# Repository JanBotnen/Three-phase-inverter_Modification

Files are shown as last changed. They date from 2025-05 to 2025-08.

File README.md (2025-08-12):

# Three-phase-inverter_Modification

**Design and implementation of a three-phase inverter with SPWM and SVPWM, prepared for future PMSM control.**

## Background
This project focuses on the continued development and modification of a three-phase DC-to-AC converter, utilizing the Space Vector Pulse Width Modulation (SV-PWM) algorithm.
The inverter was originally designed and built by a previous bachelor group at the Western Norway University of Applied Sciences, and later further refined by another group who successfully reduced the physical footprint of the design.

Their thesis can be found at:
Version 1 : [HVL Open](https://hdl.handle.net/11250/3105460)
Version 2 : [HVL Open](https://hdl.handle.net/11250/3147156)

## About the Project

Building upon their work, our bachelor group aimed to prepare the inverter for future implementation of Field Oriented Control (FOC).  
Throughout this project, our primary goal has been to implement current measurement on all three phases and enable encoder input handling for rotor position feedback.

Our thesis can be found at: 
https://hdl.handle.net/11250/3202875

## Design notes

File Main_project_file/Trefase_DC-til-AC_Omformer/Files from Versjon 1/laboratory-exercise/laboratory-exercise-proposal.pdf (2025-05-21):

# Lab - 2-nivå trefase DC/AC-omformar¹

## Emnekode: ELE119

## Emnenamn: Kraftelektronikk

## Haust 2023

Labansvarleg: Lars M. Ekroll lme@hvl.no

Emneansvarlig: Eirik Haustveit
| ehau@hvl.no

Utlevert:
dd.mm.åååå

Frist:
dd.mm.åååå
Gjennomføring:
dd.mm.åååå

Denne laboratorieoppgåva dekker grunnleggande praktisk bruk av ein 2-nivå trefase DC/AC-omformar.

Spenningane og straumane som skal nyttast i oppgåva er moderate, men framleis på eit nivå som medfører

fare. Før arbeidet kan starta er det derfor obligatorisk med ein sikkerhetsgjennomgang for alle studentar

som skal gjennomføra oppgåva.

Figur 1: 150 V, livsfare.

- 2-nivå trefase-omformar
- Romvektormodulering - SV-PWM
- Sinuspulsbreiddemodulering - SPWM

1 Denne laboratorieoppgåva er utvikla av Marius Englund, Eirik Skorve Haugland og Ingrid Hovland, med utgangspunkt i ein mal utarbeidd av Eirik Haustveit.

Lab 1 | ELE119 - Kraftelektronikk | Haust 2023

## 1 Introduksjon

Denne laboratorieoppgåva dekker 2-nivå trefase-omformar. Oppgåva er strukturert i 3 delar:

1. Forarbeid: Her skal ein berekne nokre aktuelle parameter. I tillegg skal ein simulera berekna verdiar. Resultata frå berekningar og simuleringar skal noterast i oversiktstabellen.
2. Laboratoriearbeid: Her skal ein utføre oppkoplinga, samt måling på dei fysiske modellane. Det vil være ein stor fordel om ein har gjort seg godt kjent med ein simuleringsmodell og verktøya i forkant. Grunnleggande forståing for dei to modulasjonsteknikkane SPWM og SV-PWM er og ein stor fordel. Ein skal samle måleresultat i all hovudsak ved hjelp av oscilloskop. På oscillioskopet har ein verktøy som er kjent frå Simulink, som å måla verdiar som RMS, snitt, peak-peak, FFT m.m. Ein skal også lagre datasett som CSV-filer for å kunne etterbehandla dei i Matlab. Her er det viktig at ein organiserer arbeidet, slik at ein har kontroll på kva målingar som ligg i eit gitt datasett.
3. Etterarbeid: I etterarbeidet skal ein samanlikne utrekna, simulerte og fysiske måleresultat og studere avvika som ev. viser seg. Ein skal og tolke datasett frå laboratoriearbeidet.

Arbeidet skal oppsummerast i ein enkel rapport som dokumenter dei ulike delane av oppgåva.

### 1.1 Føresetnader

Arbeidet blir utført på spenningssatt anlegg med maksimal spenning 230 V. Då dette er eit spenningsnivå som har skadepotensial for både personar og utstyr, er ein tryggleiksgjennomgang med ansvarleg for elkraft-laboratoriet, Lars M. Ekrol påkrevd før den praktiske delen av oppgåva kan gjennomførast.

### 1.2 Utstyr

Under fylgjer ei liste over utstyr som blir gjort tilgjengeleg for den praktiske gjennomføringa. Noter utstyrsnummeret du har brukt i tabell 1. Om det er avvik frå ditt oppsett skal dette avviket noterast i din rapport.

Tabell 1: Liste over utstyr til lab

Utstyr | Skildring | Utstyrsnr | Kommentar
Trafo | 2 kVA trafo, 220/133 V
Brytar | Brytar i tilførsel
Brytar | Brytar i last
Sikring | 3 fase, 2/6 A
Koblingsboks | For tilkopling og måling
Kraftmodul | 2-nivå trefase-omformar
Spenningsprobe 1 | Micsig DP1003
Spenningsprobe 2 | Micsig DP1003
Strømtang 1 | Micsig CP2100A
Strømtang 2 | Micsig CP2100A
Multimeter | Hioki DT4282
| Koplingsleidningar med bananplugg
Effektmotstand | Belastningsmotstand
Effektmotstand | Straumbegrensingsmotstand for kondensator

Side 1 av 8

Lab 1 | ELE119 - Kraftelektronikk | Haust 2023

### 1.3 Måleinstrument

For å gjennomføra denne laboratorieoppgåva er det nødvendig å ha kjennskap til dei måleinstrumenta ein skal nytta. I all hovudsak skal oscilloskop nyttast til målingane, men det kan og vera aktuelt å foreta enkelte målingar med multimeter. Figur figur 2 viser oscilloskopet som skal nyttast. Det føresett grunnleggande forkunnskap i å bruka oscilloskopet, som justering av skallering, tid, størrelse, trigger og liknande. Vedlegg A gir ei enkel innføring i korleis ein stillar in probar, samt korleis ein hentar ut relevante målingar.

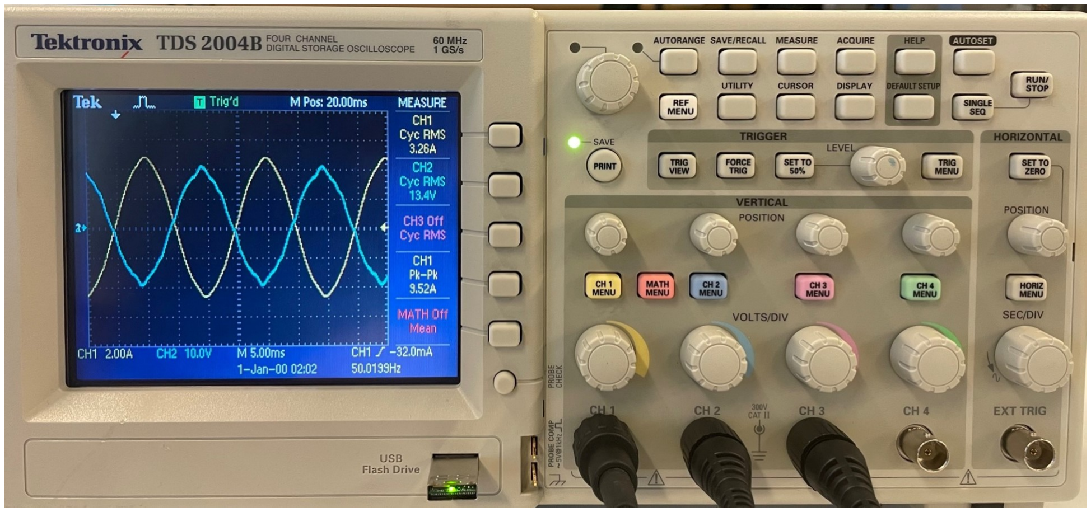
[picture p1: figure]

Figur 2Bilde av oscilloskop, Tektronix TDS 2004B

Side 2 av 8

Lab 1 | ELE119 - Kraftelektronikk | Haust 2023

## 2 2-nivå trefase-omformar

Oppgåve 1
I denne oppgåva skal de gjera målingar på ein 2-nivå trefase-omformar. Omformaren består av ein DC-link og seks transistorar som kan verta styrt med forskjellige modulasjonsteknikkar. I denne oppgåva skal dei to modulasjonsteknikkane sinuspulsbreiddemodulasjon (SPWM) og romvektormodulasjon (SV-PWM) samanliknast.

Tilført spenning Us = 150 V med frekvensen f1 = 50 Hz.

Forarbeid:
(a) Utfør berekning av verdiar gitt i tabell 2 for SPWM og SV-PWM.
(b) Simuler verdiane gitt i tabell 2.

Laboratoriearbeid:
Dei akutelle “measure” verdiane frå skopet skal noterast i tabell 2.
(a) Kontroller at du har tilgong på nødvendig utstyr, og kople opp omformaren mot last. Alle
| målingane skal gjerast for både SPWM og SV-PWM.
(b) Skru på DC-link spenning og svitsjing i mikrokontroller ved å trykke start på kortet. Observer tilført og avgitt spenning på oscilloskopet. Du skal bruka “measure” funksjonen i skopet til å finna frekvens, snitt, peak-peak og RMS verdi av målingane. Vidare skal du lagra eit datasett av målingane til ein minnepinne. For referanse skal PWM frå mikrokontroller vera med på alle målingar frå skopet.
i. Foreta ei samtidig måling av tilført, samt avgitt spenning. Noter “measure” verdiane.
| ii. Foreta ei måling av tilført, samt avgitt straum. Noter “measure” verdiane.
iii. Foreta ei samtidig måling av tilført straum og spenning. Bruk “math” funksjonen i skopet til å finna effektkurva og ta snittet av denne kurva for å finna aktiv effekt. Noter “measure” verdiane.
iv. Foreta ei samtidig måling av avgitt straum og spenning. Bruk “math” funksjonen i skopet til å finna avgitt aktiv effekt. Noter “measure” verdien av snittet til den berekna effektkurva.
v. Mål det harmoniske innhaldet i spenning.

Etterarbeid:
(a) Vurder kva som er årsaka, dersom det er nokon ruter i tabellen som står tomme. Kvifor er dette verdiar som er vanskelig å berekna, eller å måla fysisk? Dersom du har fyllt ut heile tabellen,
| treng du ikkje svare på denne oppgåva.
(b) Vurder årsaker til avvik mellom berekningar og fysiske målingar. Ta omsyn til toleransar i
| måleinstrument, og ikkje-ideelle eigenskapar ved diodane.
(c) Samalikn kurvene frå datasetta til SPWM og SV-PWM. Kva er årsaken til likheitar og ulikheitar?
(d) Samanlikn målte og simulerte resultat av dei to modulasjonsteknikkane.

Side 3 av 8

Lab 1 | ELE119 - Kraftelektronikk | Haust 2023

Tabell 2. Samanlikning mellom berekna, simulerte, og målte verdiar

| | | SPWM | | | SV-PWM
Storleik | Skildring | Kalk. | Sim. | Målt | Kalk. | Sim. | Målt
U¯
d | Avgitt snittspenning
Ud | Avgitt RMS spenning
¯Id | Avgitt snittstraum
∆Ud | Rippel i avgitt spenning
Us | Tilført RMS spenning | 150 V | 150 V | | 150 V | 150 V
Is | Tilført RMS straum
Is1 | Grunnharmonisk RMS straum
Is3 | RMS av 3 harmoniske i tilført straum
THDi | THD i tilført straum
Pd | Avgitt aktiv effekt | X | | | X
Ps | Aktiv effekt frå Us | X | | | X
PF | Total effektfaktor | X | | | X

Side 4 av 8

## A Innstilling og bruk av oscilloskop

Dette vedlegget gir ei kort inføring i det oscilloskopet, samt dei måleprobane ein skal nytta i denne laboppgåva.

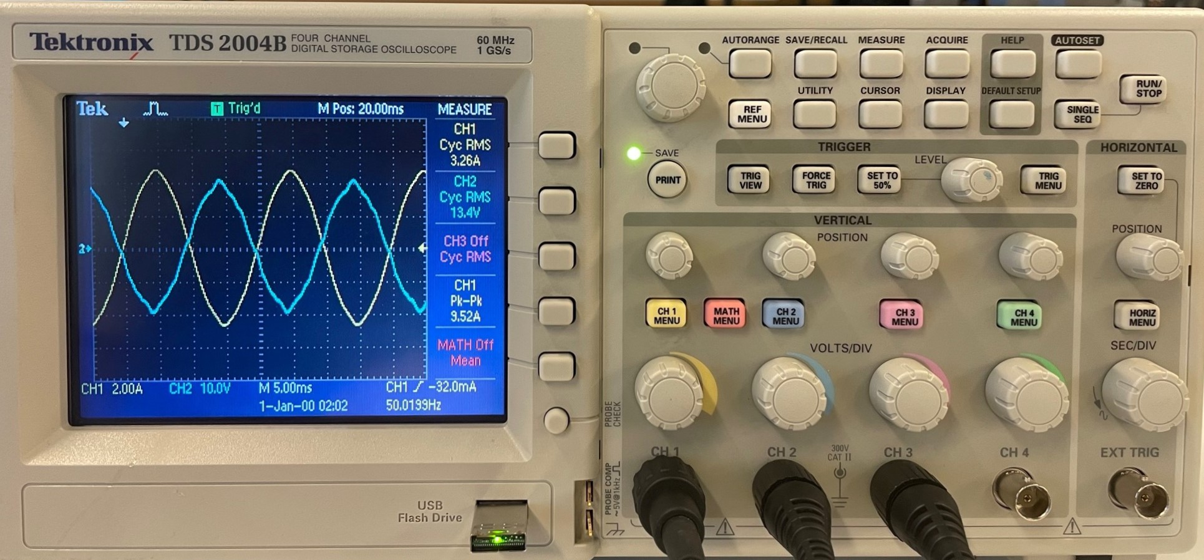
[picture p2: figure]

Figur 3Bilde av oscilloskop, Tektronix TDS 2004B

A.1 Differensialprobe for spenningsmåling

Differensialproben Micsig DP10013 skal brukast til spenningsmåling og kan operera opptil 1,3 kV. Proben kan stillast på 2 måleområder, X50/X500, og ein må velga det området som passar best for dei spenningane ein forventer å måla. For riktig avlesing på oscilloskopet må ein stilla det inn på det samme måleområdet som proben.

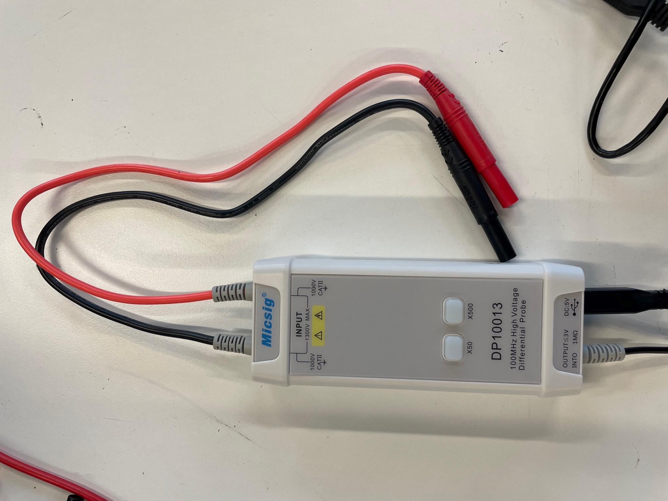
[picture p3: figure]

Figur 4Bilde av differensialprobe for spenningsmåling, Micsig DP1003

Frå kanal menyen “CH X MENU” får ein individuelle valg per kanal i sidemenyen. “Coupling”, skal vera DC. For spenningsproben velger ein “Voltage” og “Attenuation” 50X eller 500X avhengig av din probeinnstilling.

A.2 Tangamperemeter for straummåling

Straumtanga Micsig CP2100A skal brukast til straummåling og kan operere opptil 100 A. Proben kan stillast på 2 måleområder, 10 eller 100 A.
Frå kanal menyen “CH X MENU” får ein individuelle valg per kanal i sidemenyen. “Coupling”, skal vera DC. For straumtanga velger ein “Current” og “Scale” etter minste måleområde, 100 mV/A. Sjekk at straumtanga lyser på 10 A måleområde. Når skalering er utført kan ein nullstille straumtanga ved å trykke “Zero” og evt. justere DC-offset med pilene dersom den ikkje viser 0 A før du begynner å ta målingar.

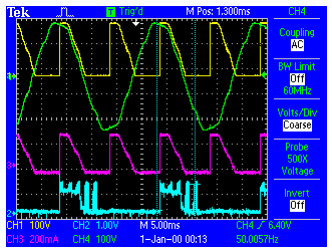
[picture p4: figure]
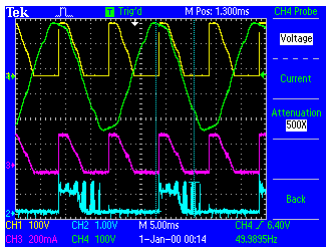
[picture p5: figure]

(a) Sidemeny etter valg av “CH X MENU”. | (b) Sidemeny etter valg av “Probe”

Figur 5Instilling av spenningsprobe

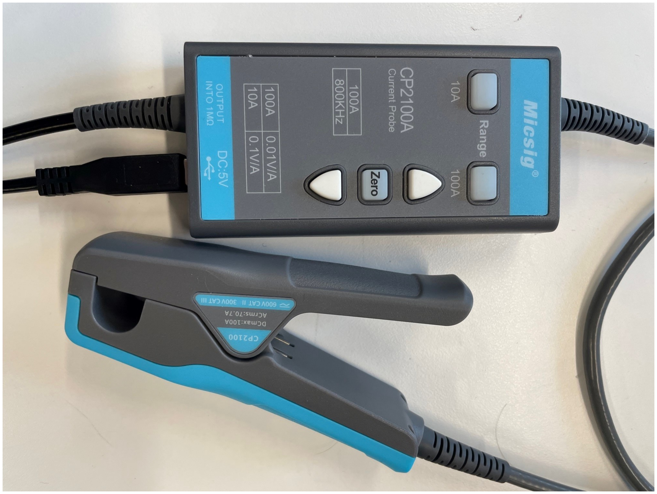
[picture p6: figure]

Figur 6Bilde av strømtang, Micsig CP2100A

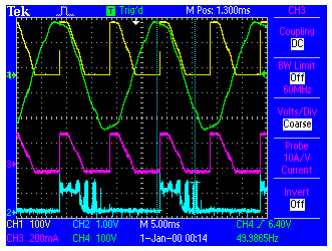
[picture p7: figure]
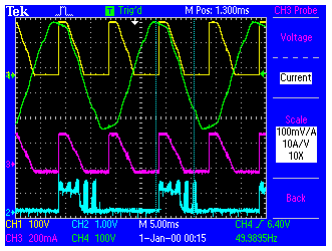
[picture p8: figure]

(a) Sidemeny etter valg av “CH X MENU” | (b) Sidemeny etter valg av “Probe”

Figur 7Instilling av straumtang

A.3 Målingar på skop

Oscilloskopet har ein “measure”-funksjon som kan gi oss forskjellige verdiar ut frå dei kurvene me måler. Denne funksjonen skal me nytta til å henta ut RMS, snitt, peak-peak og frekvens. For å definere målingar mot gitt kanal trykker ein på “measure” og velger målepunkt i sidemenyen. Frå sidemenyen velger ein spesifikk kanal og kan vidare definere kjelde, og målefunksjon.

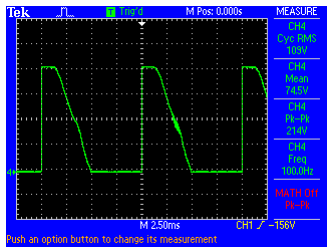
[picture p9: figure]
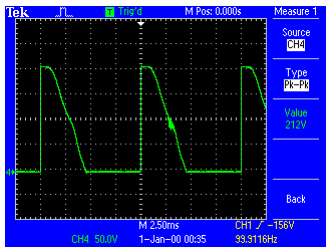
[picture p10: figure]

(a) Sidemeny etter valg av “Measure” | (b) Sidemeny etter valg av spesifik måling

Figur 8Instilling av målingar som RMS, snitt, peak-peak, frekvens med fleire

A.4 Bruk av “cursors” på skop

“Cursors” kan nyttast for å sjå dei forskjellige kurvene i relasjon til kvar andre, eller for å finna relasjonen mellom forskjellige punkt på den samme kurva. Ein kan avlesa distanse i tid, eller i spenning eller straum. For å aktivera trykker ein på “Cursors” og velger type og kanal. Ein velger mellom dei 2 målelinjene, “Cursors”, i sidemenyen og kan flytte disse individuelt med multi-purpose hjulet. Punktavlesning per målelinje kan lesast av samt differansen mellom dei 2 målelinjene.

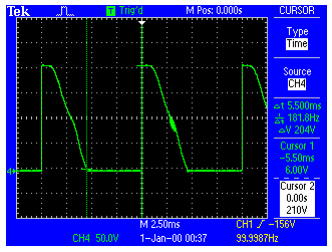
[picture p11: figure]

(a) Vertikale “Cursors” for punktavlesning og tidsdifferanse

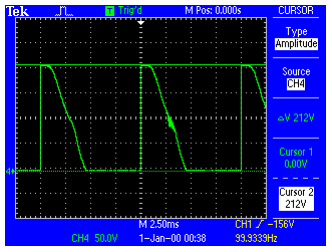
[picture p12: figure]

(b) Horistontale “Cursors” for punktavlesning og amplitudedifferanse

Figur 9Bruk av “Cursors” til måling av signal

A.5 Matte-funksjonar

Ein kan bruke scopet til å rekne ut samanhengar mellom kanalar samt gjera nokre analysar per kanal. For å berekne effekt kan ein multiplisere straum og spenning ved å trykker på “MATH MENU” ved å velge X i operasjon fra sidemenyen. Matte-funksjonen kan vidare hentast inn i “Measure” bildet
Ein kan og gjere måling av harmonisk spekter for ein kanal ved å trykker på “MATH MENU” ved å velge kilde referert til kanal, source, samt FFT frå sidemenyen. Ein kan i dette bildet bruke “Cursors” til å lese av frekvens/amplitude.
Figur 11 viser eit døme på FFT-bilde frå skopet.
FFT målingane på Tektronix TDS 2004B er oppgitt i desibel relativt til ei RMS spenning på 1 V. Den fylgjande formelen syner samanhengen mellom spenning og desibel:

dBV = 20 log
U

1 V
(1)

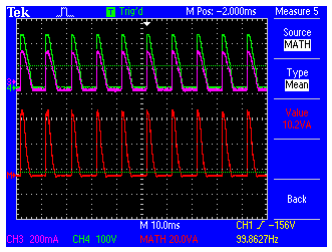
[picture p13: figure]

(a) Sidemeny og effektkurve etter valg av “Measure” mot mattefunksjon

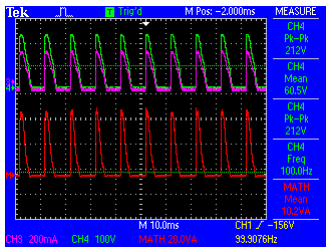
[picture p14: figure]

(b) Sidemeny inkludert målingar og mattefunksjon

Figur 10Bruk av mattefunksjon til å multiplisere straum og spenning

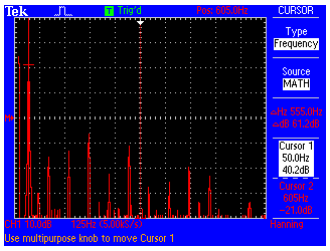
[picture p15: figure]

Figur 11FFT-måling

A.6 Total harmonisk forvrenging

Det er ikkje vanleg at oscilloskopet har innebygd støtte for berekning av total harmonisk forvrenging. Det er derimot mulig å berekna verdien frå dei harmoniske komponentane ein finn i spektrumsanalysatoren.

THDu =

p
U

2
2 + U

2
3 + U

2
4 + . . .
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
+ . . . | (2)

Differansen mellom den grunnharmoniske og ein overharmonisk komponent kan uttrykkast som:

dBc = 10 · log
P
Pc
(3)

Der P er den overharmoniske og Pc er den grunnharmoniske (carrier). Denne verdien kan normalt finnast ved å plassera ein "cursorpå den grunnharmoniske, og ein anna "cursorpå den overharmoniske komponenten som er av interesse. Verdien ein er ute etter er ofte uttrykt som ∆dB.

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
= 10

dBc
10

(5)

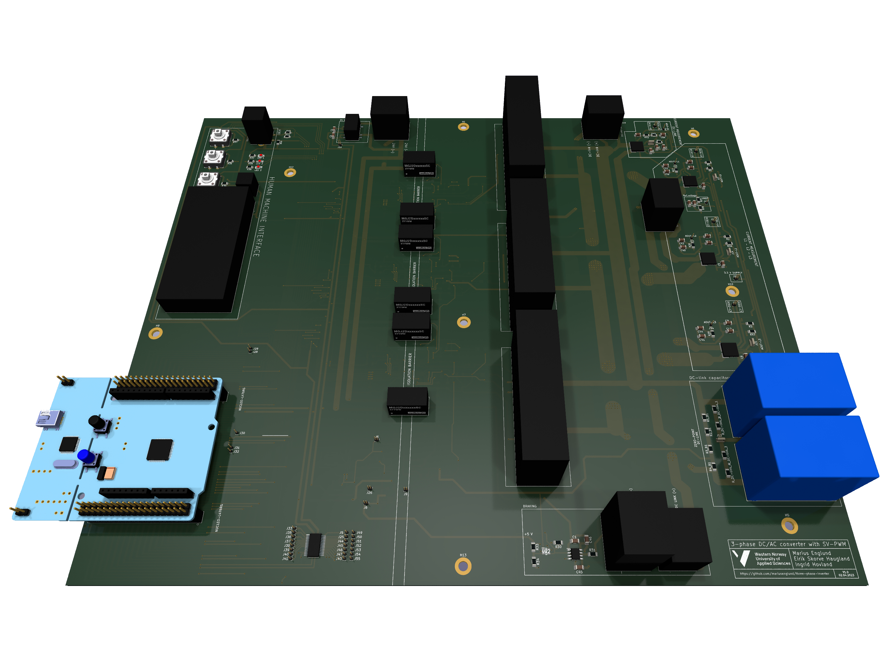
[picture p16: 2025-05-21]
Main_project_file/Trefase_DC-til-AC_Omformer/Files from Versjon 1/img/3d-model-front.png

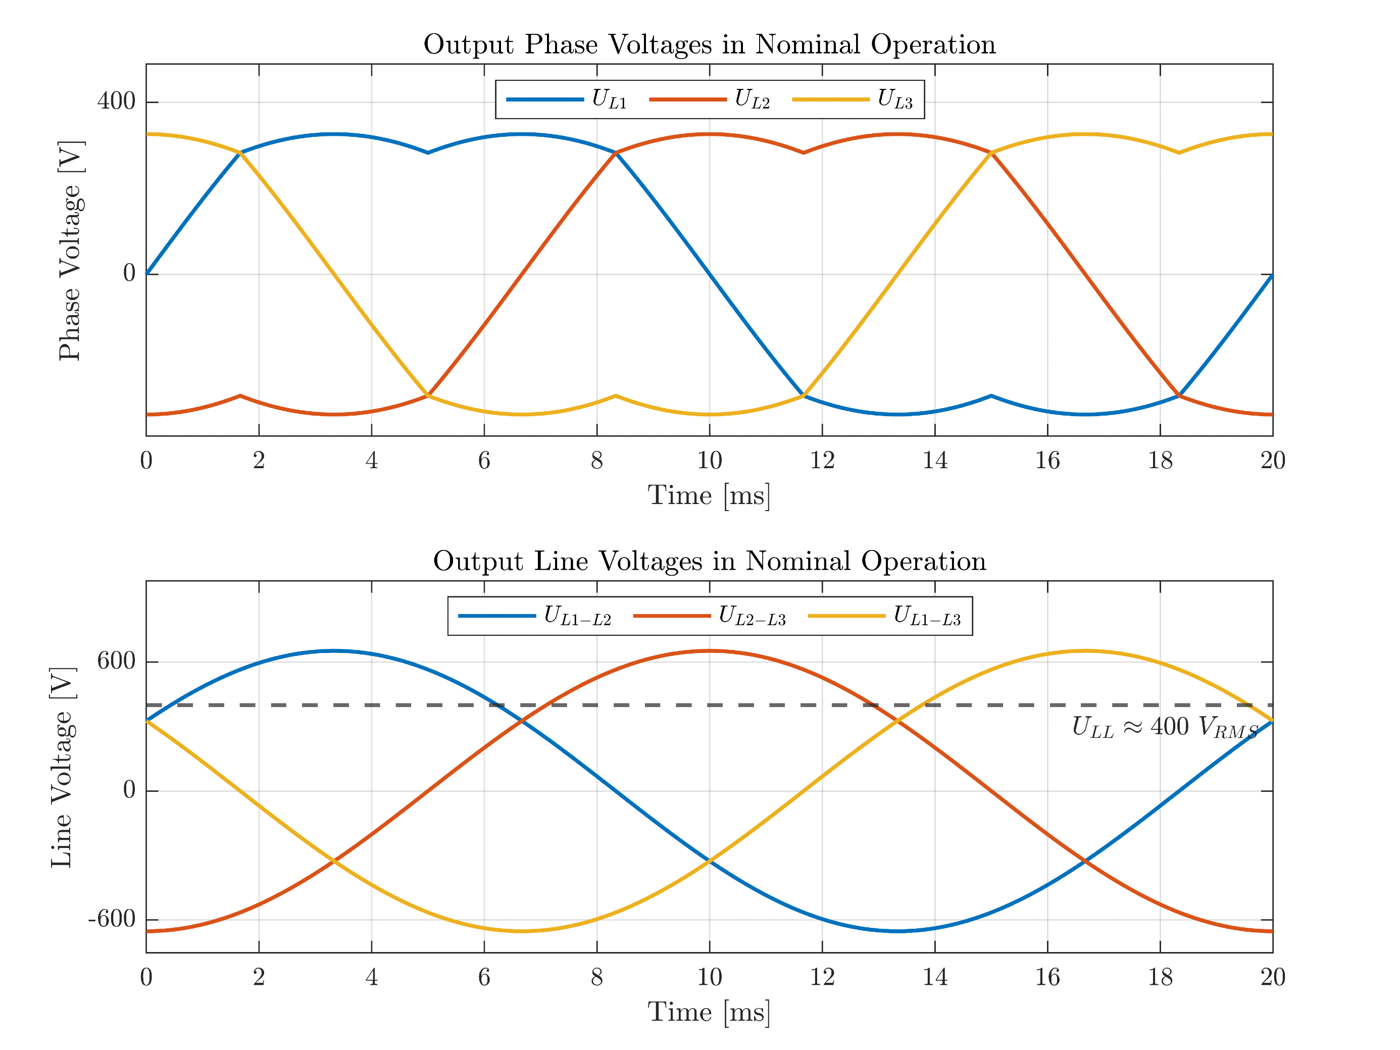
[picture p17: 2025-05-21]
Main_project_file/Trefase_DC-til-AC_Omformer/Files from Versjon 1/img/space-vector-voltages.png

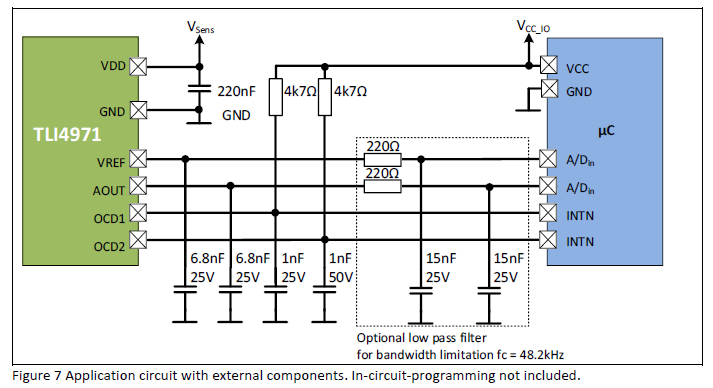
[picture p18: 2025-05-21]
Main_project_file/Trefase_DC-til-AC_Omformer/Files from Versjon 1/Koblingsskjemaer/Strømsensor_kobling.png

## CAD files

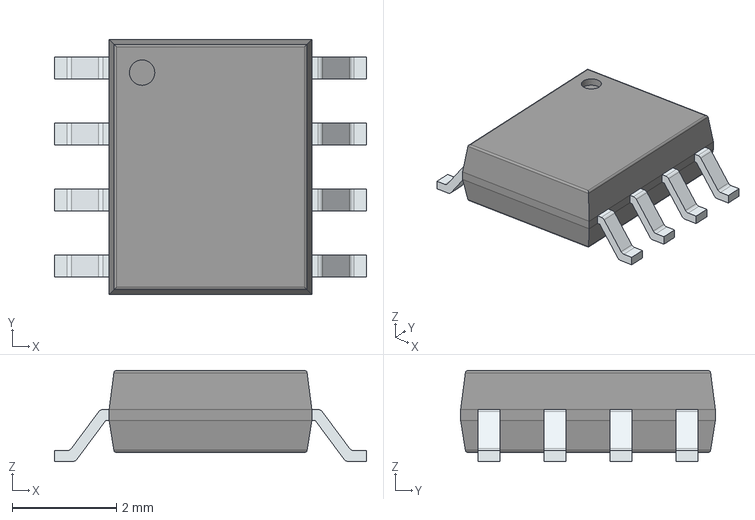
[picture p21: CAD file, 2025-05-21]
Main_project_file/Trefase_DC-til-AC_Omformer/pcb-design-files_v3/LIB-3D/IR2118SPBF.stp
6.00 x 4.90 x 1.75 mm
PinsArrayLR

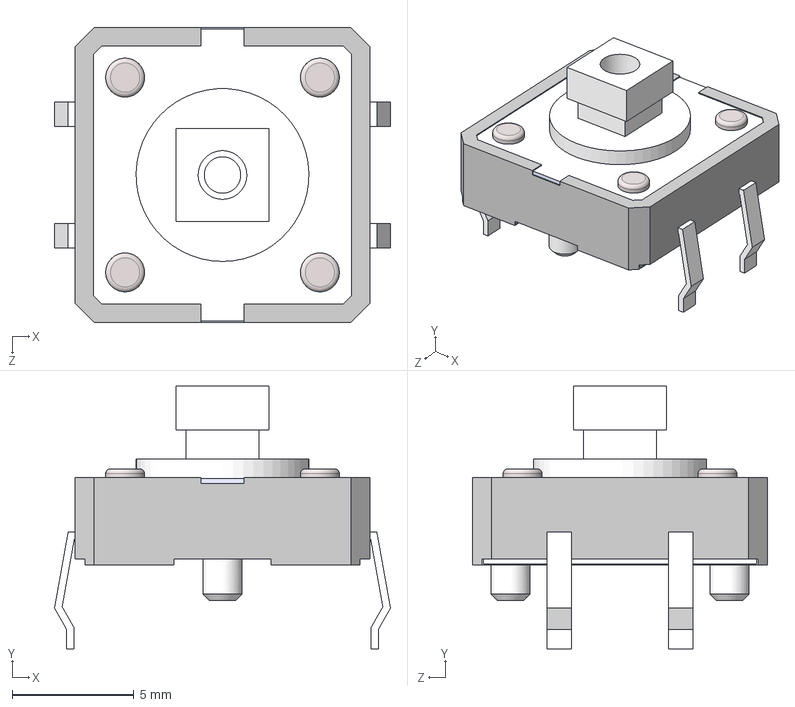
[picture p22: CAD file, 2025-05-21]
Main_project_file/Trefase_DC-til-AC_Omformer/pcb-design-files_v3/LIB-3D/B3F-5050.stp
13.8 x 10.8 x 12.1 mm

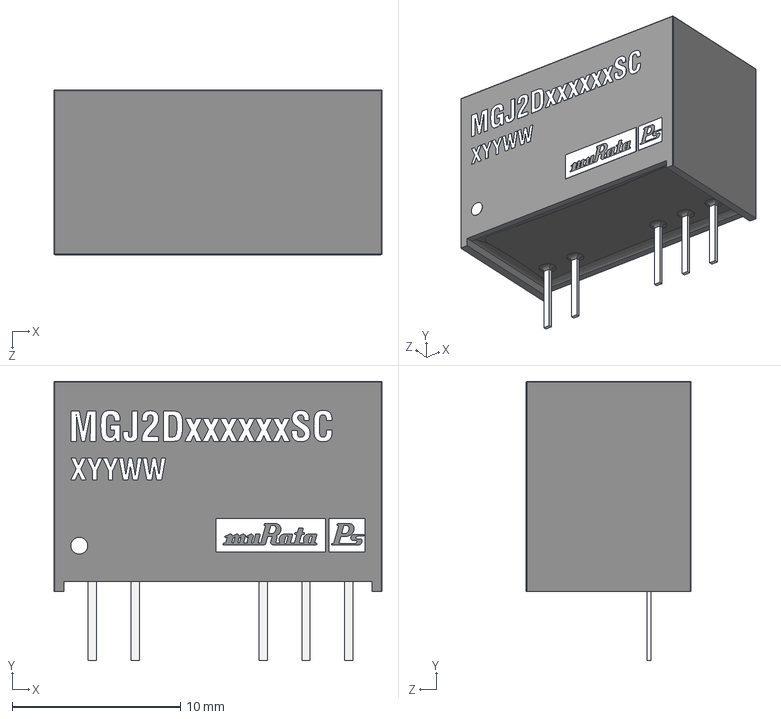
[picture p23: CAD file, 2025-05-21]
Main_project_file/Trefase_DC-til-AC_Omformer/pcb-design-files_v3/LIB-3D/MGJ2D241509SC.stp
19.5 x 16.6 x 9.82 mm

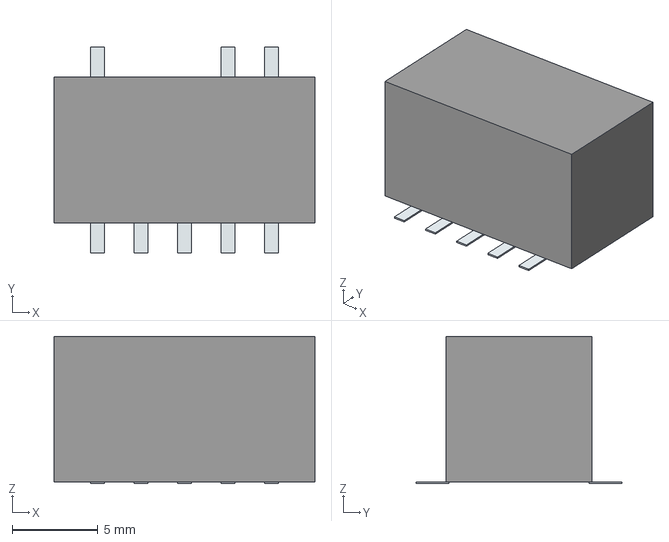
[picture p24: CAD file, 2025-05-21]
Main_project_file/Trefase_DC-til-AC_Omformer/pcb-design-files_v3/LIB-3D/MP-K7803T-500R3.stp
15.2 x 12.0 x 8.60 mm
Pins

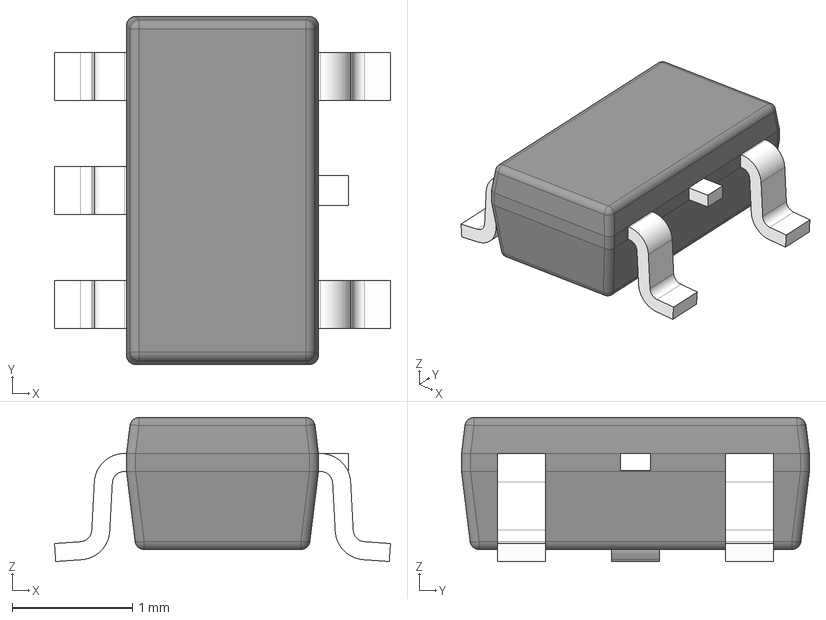
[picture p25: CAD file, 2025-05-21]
Main_project_file/Trefase_DC-til-AC_Omformer/pcb-design-files_v3/LIB-3D/LMV331M5.stp
2.80 x 2.90 x 1.20 mm
BODY-SOT
LEAD-SOT x 5
LEAD-DUMMY

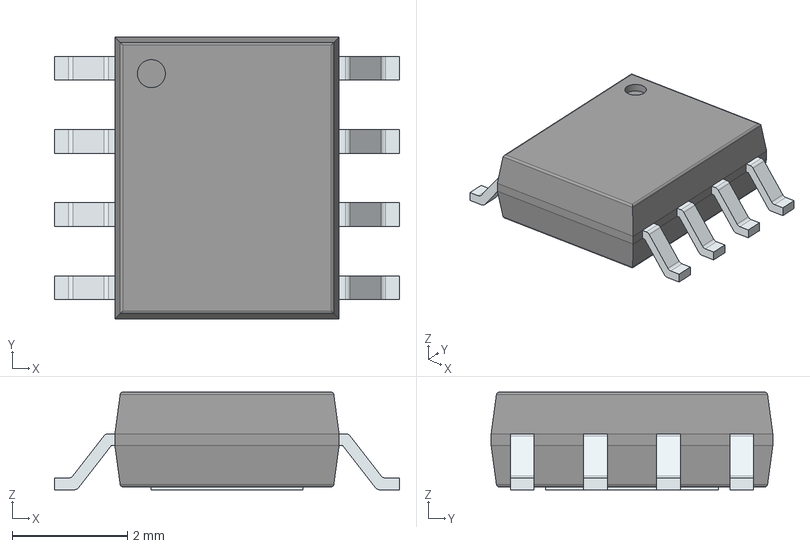
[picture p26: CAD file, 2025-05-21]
Main_project_file/Trefase_DC-til-AC_Omformer/pcb-design-files_v3/LIB-3D/TLS205B0EJV33XUMA1.stp
6.00 x 4.90 x 1.70 mm
PinsArrayLR
ThermalPad

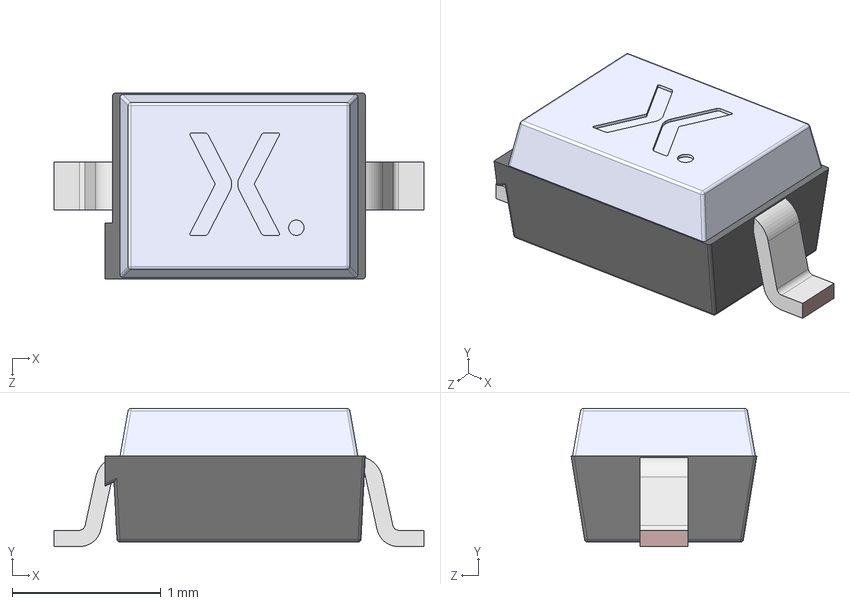
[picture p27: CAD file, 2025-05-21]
Main_project_file/Trefase_DC-til-AC_Omformer/pcb-design-files_v3/LIB-3D/Schottky-BAT165AX.stp
2.49 x 0.93 x 1.25 mm
SOD323 Lower body
SOD323 Lead x 2
SOD323 Upper body

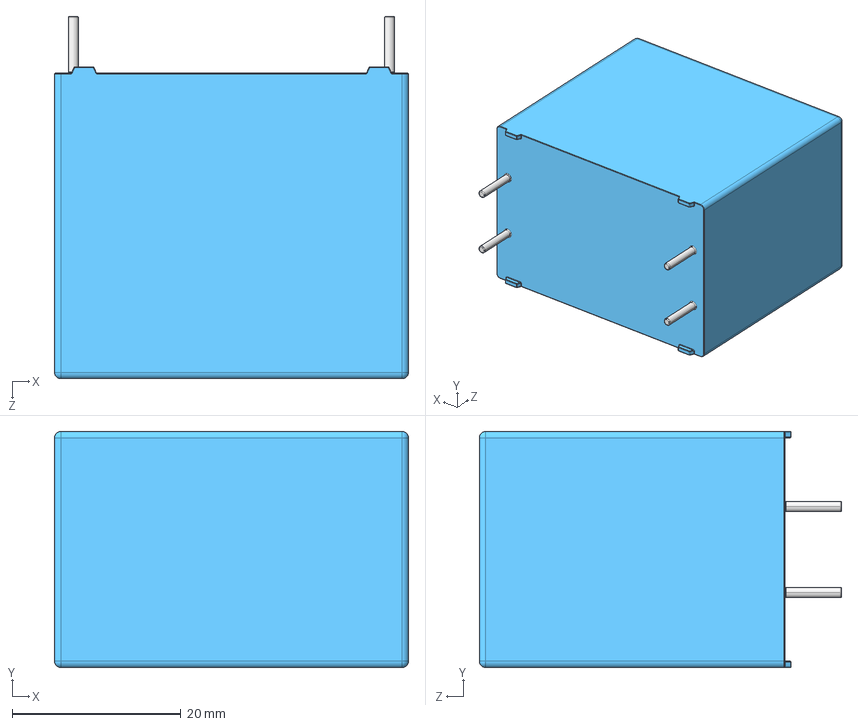
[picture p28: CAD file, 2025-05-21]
Main_project_file/Trefase_DC-til-AC_Omformer/pcb-design-files_v3/LIB-3D/DC-link-capacitor-B32776G0146K000.stp
42.0 x 28.0 x 43.0 mm

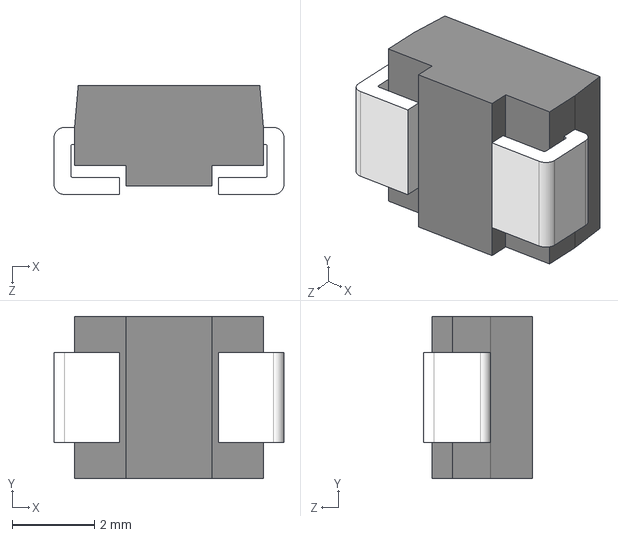
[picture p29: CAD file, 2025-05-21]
Main_project_file/Trefase_DC-til-AC_Omformer/pcb-design-files_v3/LIB-3D/Diode-STTH112U.stp
5.60 x 3.95 x 2.65 mm

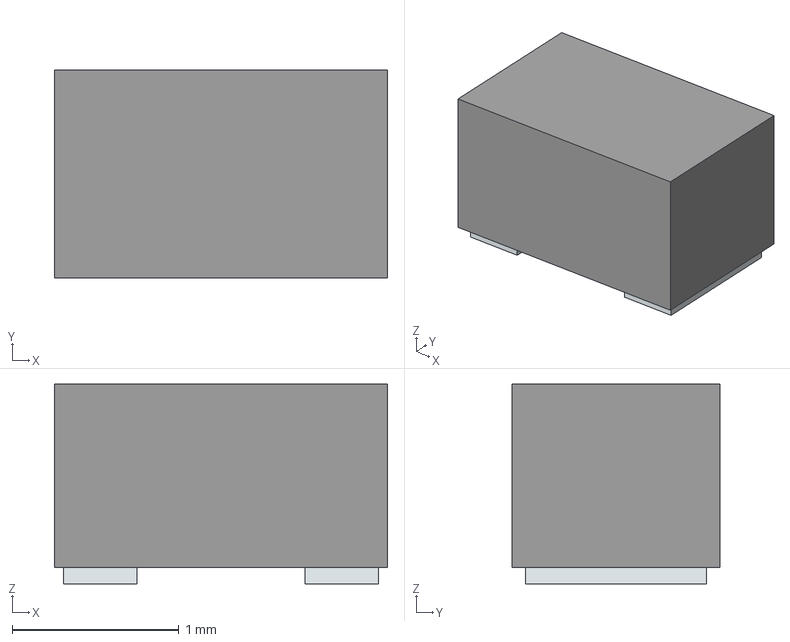
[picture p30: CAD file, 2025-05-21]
Main_project_file/Trefase_DC-til-AC_Omformer/pcb-design-files_v3/LIB-3D/LED_yellow_SML-LX0805SYC-TR.stp
2.00 x 1.25 x 1.20 mm
Pins

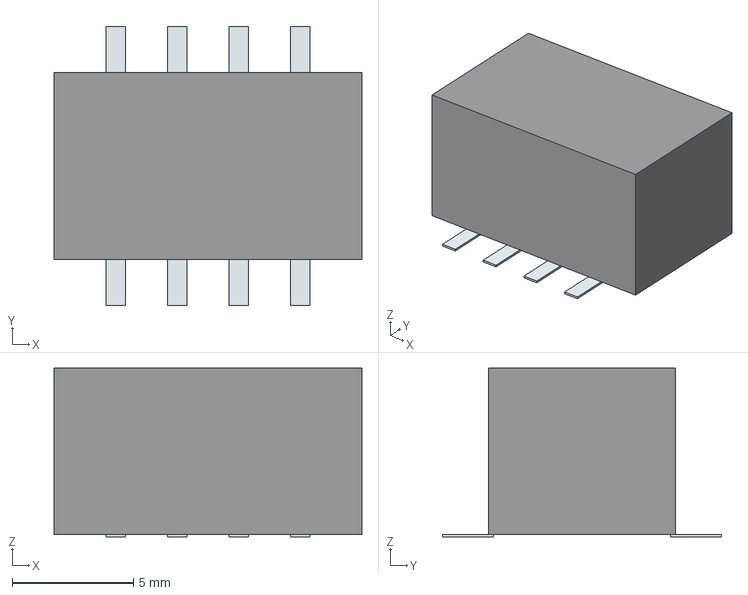
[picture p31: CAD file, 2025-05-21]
Main_project_file/Trefase_DC-til-AC_Omformer/pcb-design-files_v3/LIB-3D/NTE0505MC.stp
12.7 x 11.5 x 6.95 mm
Pins

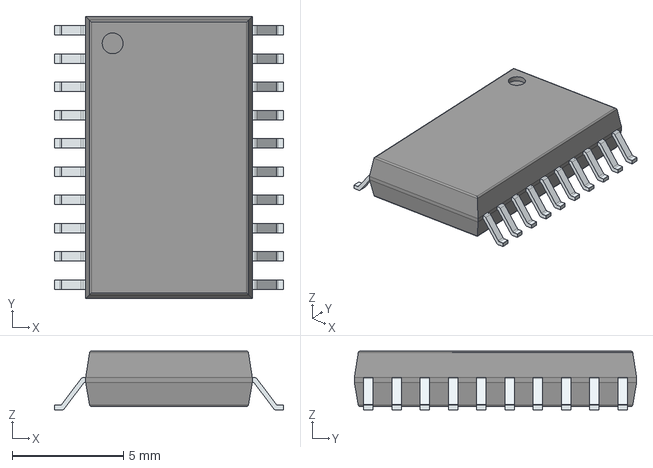
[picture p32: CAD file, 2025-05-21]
Main_project_file/Trefase_DC-til-AC_Omformer/pcb-design-files_v3/LIB-3D/1ED020I12FA2XUMA2.stp
10.3 x 12.7 x 2.65 mm
PinsArrayLR

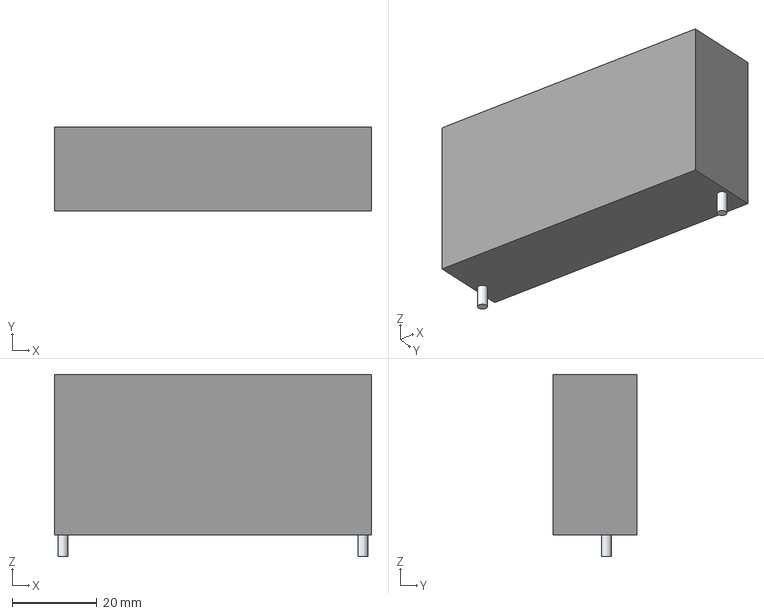
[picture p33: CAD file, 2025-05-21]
Main_project_file/Trefase_DC-til-AC_Omformer/pcb-design-files_v3/LIB-3D/Heatsink_C247-075-3AE.stp
75.0 x 19.9 x 43.1 mm
Leads x 2

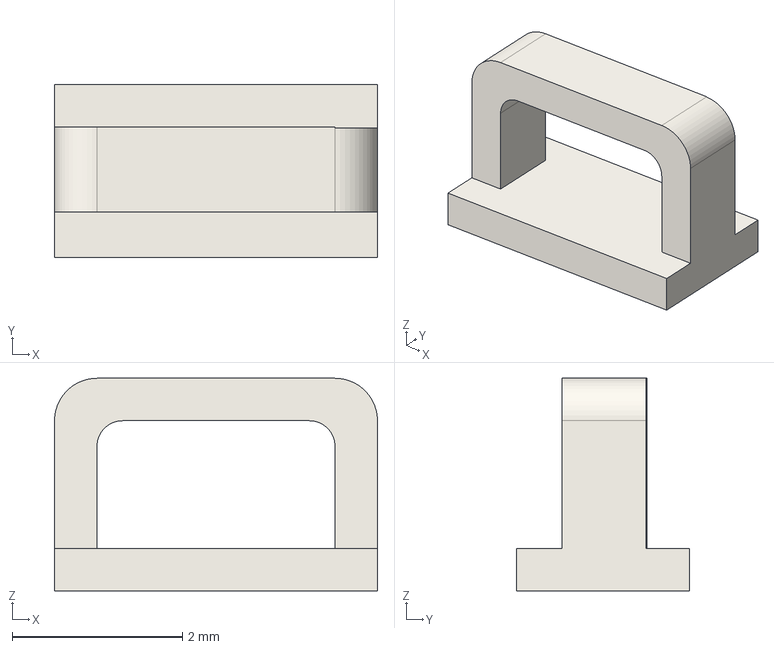
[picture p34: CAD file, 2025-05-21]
Main_project_file/Trefase_DC-til-AC_Omformer/pcb-design-files_v3/LIB-3D/Keystone - 5019 - PCB Test Point v1.step
3.80 x 2.03 x 2.50 mm

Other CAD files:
Main_project_file/Trefase_DC-til-AC_Omformer/pcb-design-files_v3/LIB-3D/C247-025-1VE.stp
Main_project_file/Trefase_DC-til-AC_Omformer/pcb-design-files_v3/LIB-3D/Encoder_EC12E2424407.stp
Main_project_file/Trefase_DC-til-AC_Omformer/pcb-design-files_v3/LIB-3D/OPA237NA_250.stp
Main_project_file/Trefase_DC-til-AC_Omformer/pcb-design-files_v3/LIB-3D/ACPL-C87B-000E.stp
Main_project_file/Trefase_DC-til-AC_Omformer/pcb-design-files_v3/LIB-3D/61304021821.stp
Main_project_file/Trefase_DC-til-AC_Omformer/pcb-design-files_v3/LIB-3D/74LV1T34GV-Q100H.stp
Main_project_file/Trefase_DC-til-AC_Omformer/pcb-design-files_v3/LIB-3D/Display_MC21605C6W-SPTLYI-V2.stp
Main_project_file/Trefase_DC-til-AC_Omformer/pcb-design-files_v3/LIB-3D/IKW40N120H3.stp
Main_project_file/Trefase_DC-til-AC_Omformer/pcb-design-files_v3/LIB-3D/LED_red_SML-LX0805SIC-TR.stp
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

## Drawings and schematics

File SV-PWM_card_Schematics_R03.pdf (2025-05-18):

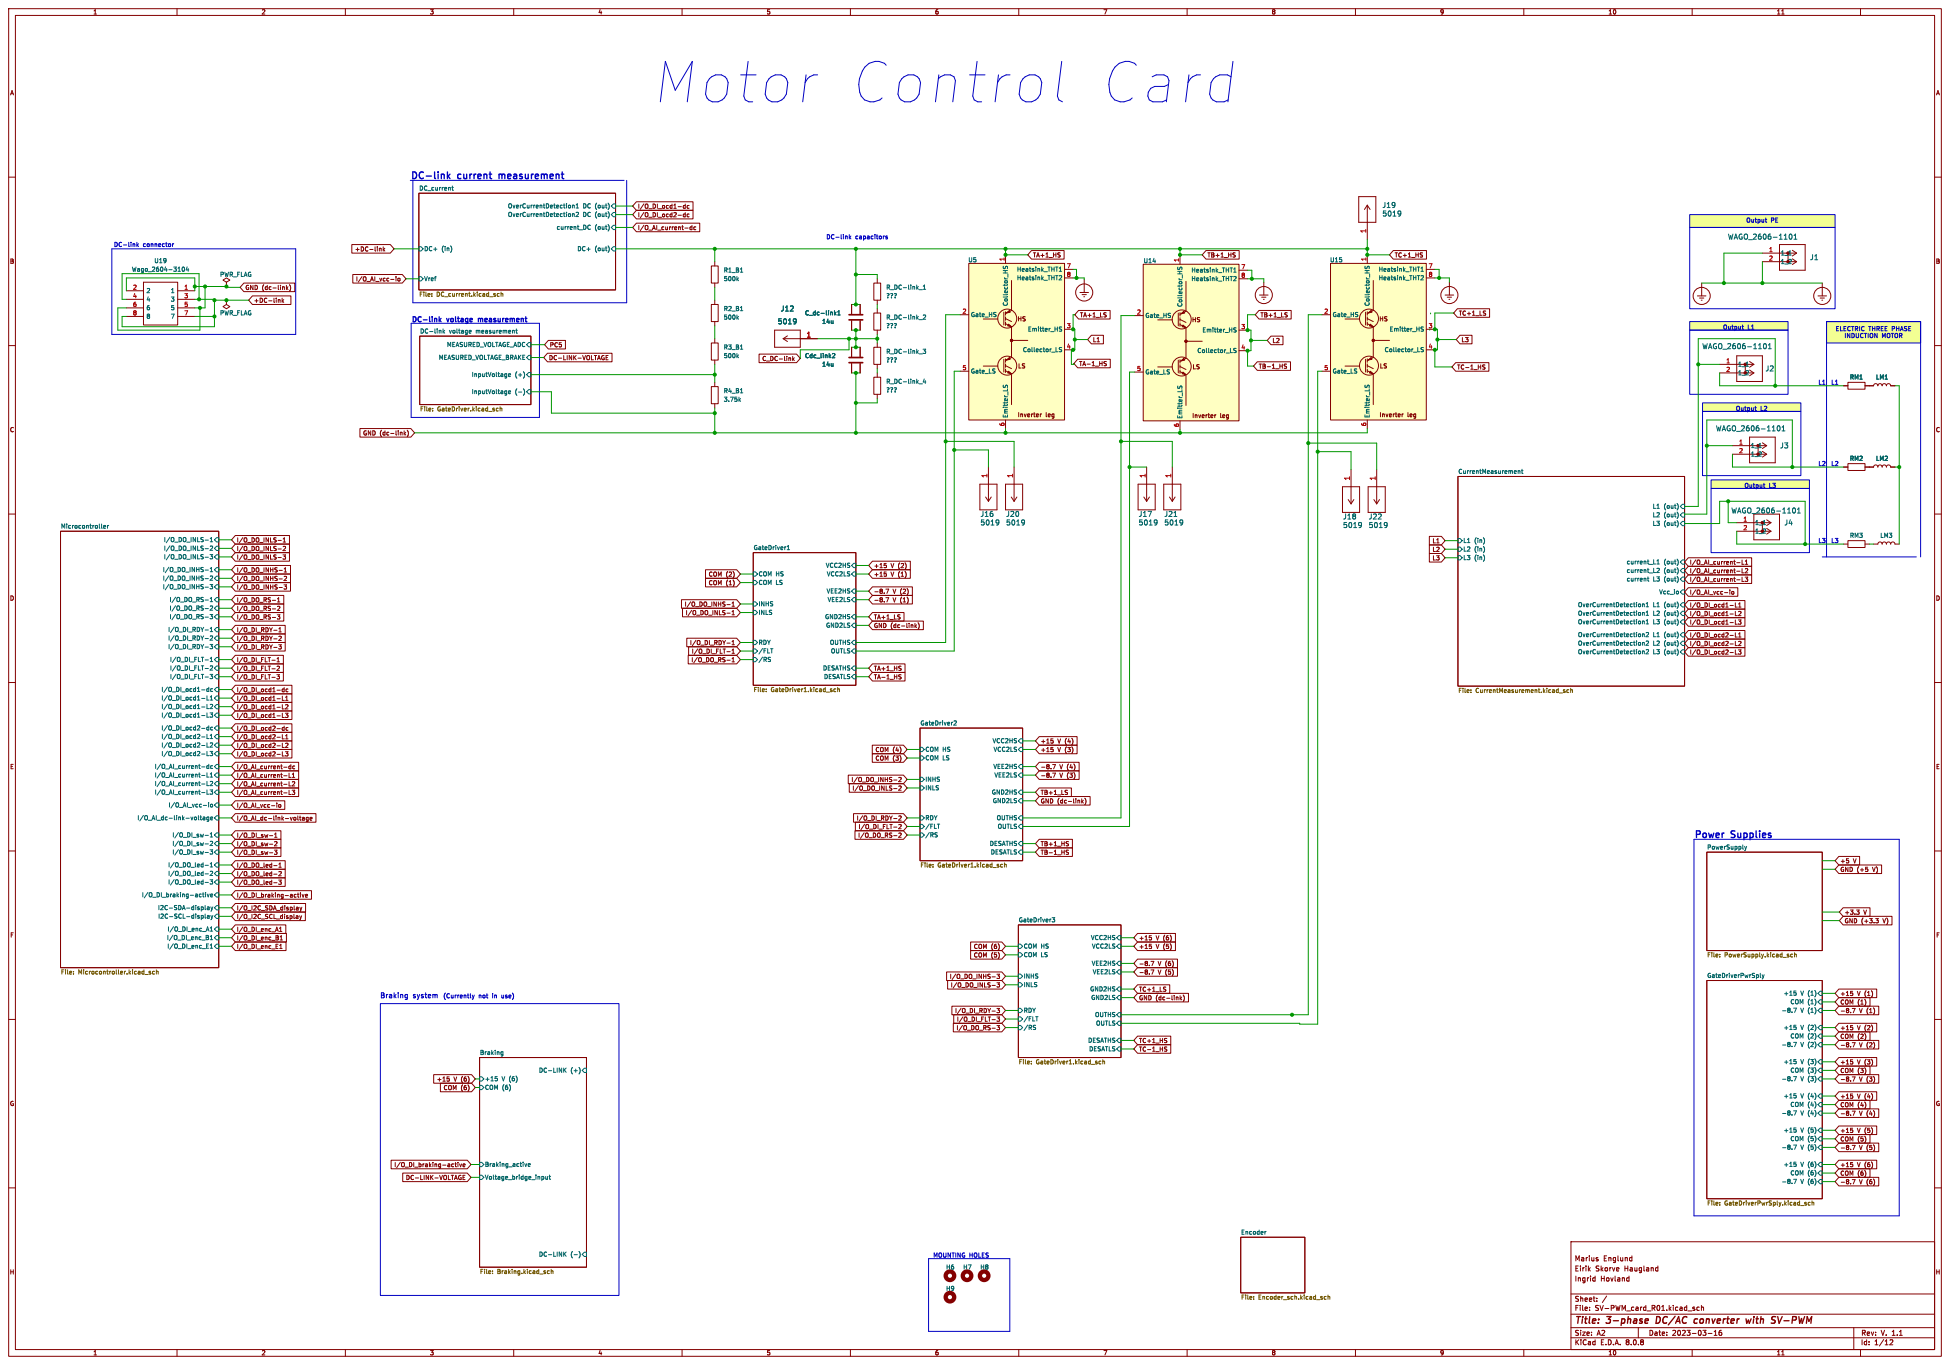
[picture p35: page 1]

GND (dc-link) +DC-link

GND (dc-link) TA+1_LS

VCC2LS OUTLS DESATHS DESATLS COM LS COM HS GateDriver3 File: GateDriver1.kicad_sch
VCC2HS OUTHS GND2HS

I/O_DO_INLS-3 COM (6) +15 V (6)
Braking File: Braking.kicad_sch
DC-LINK (+) DC-LINK (-)

I/O_DI_braking-active DC-LINK-VOLTAGE

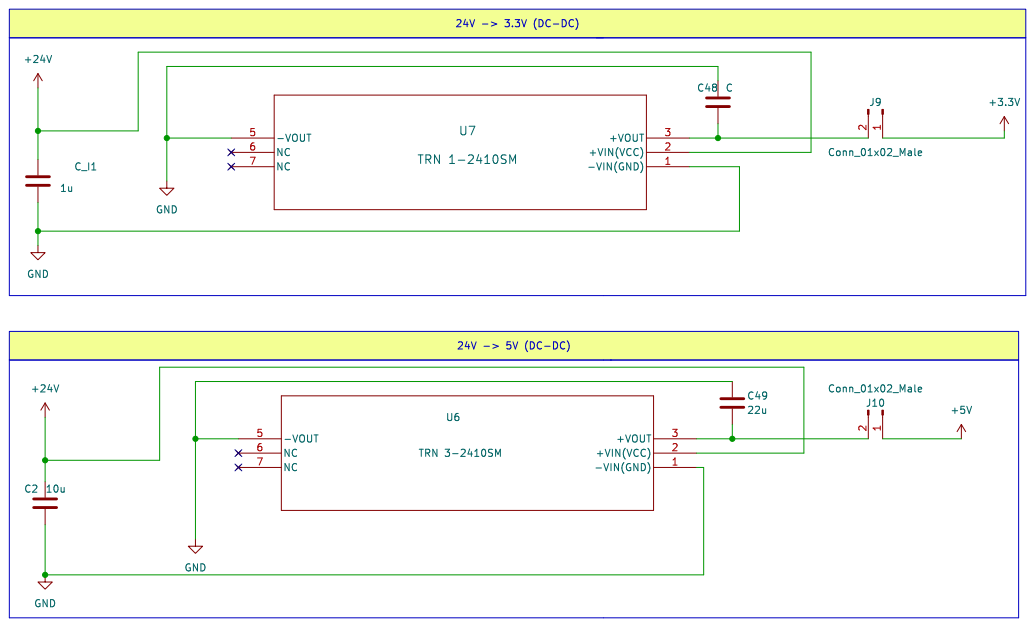
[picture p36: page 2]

File: PowerSupply.kicad_sch Sheet: /PowerSupply/

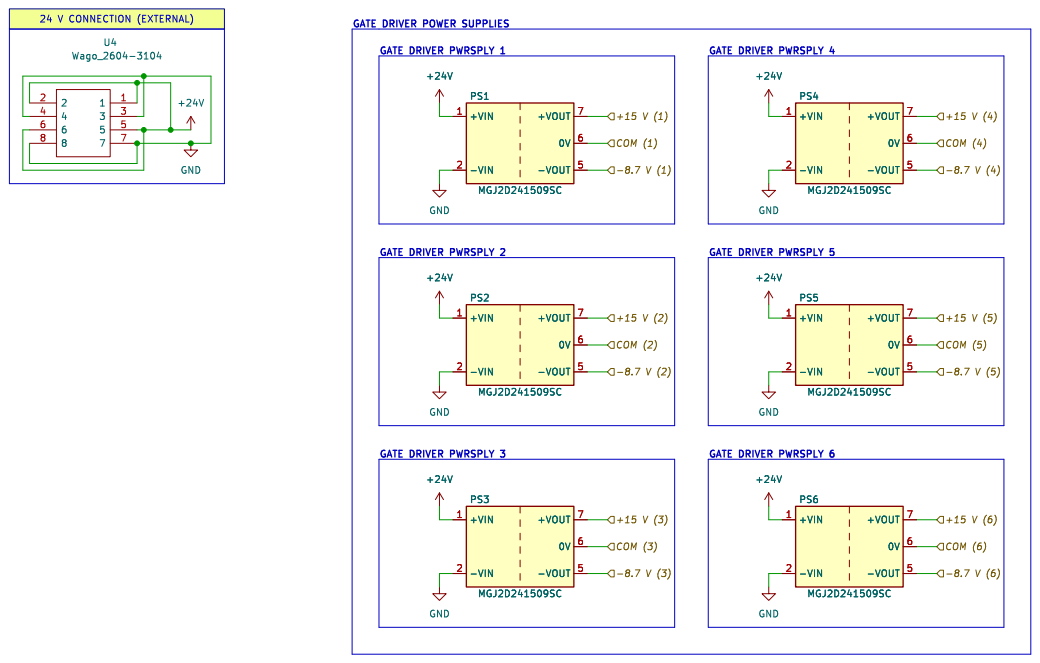
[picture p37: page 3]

File: GateDriverPwrSply.kicad_sch Sheet: /GateDriverPwrSply/

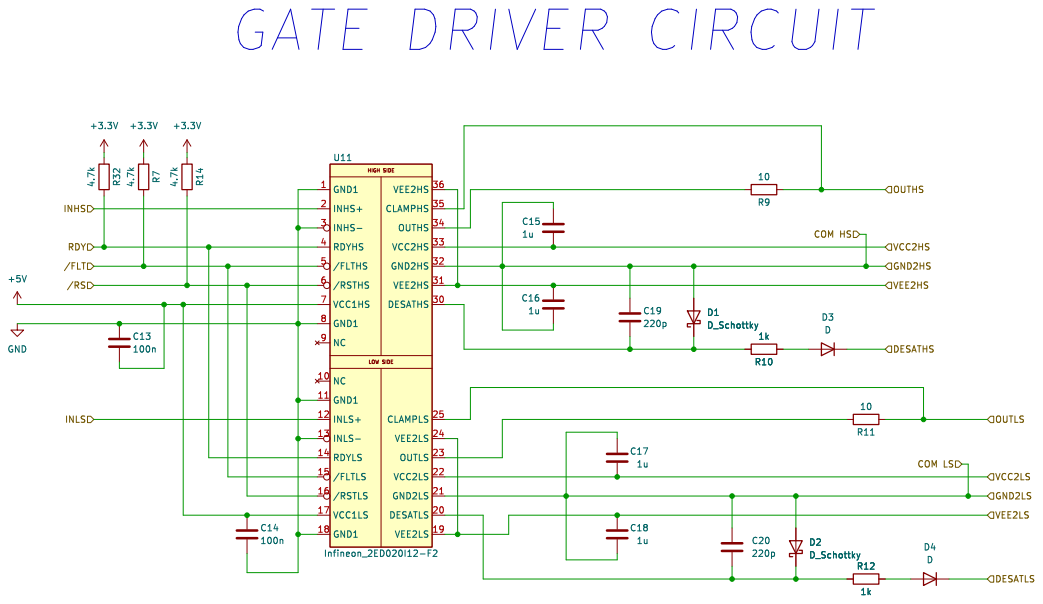
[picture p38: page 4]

VCC2HS OUTHS GATE DRIVER CIRCUIT

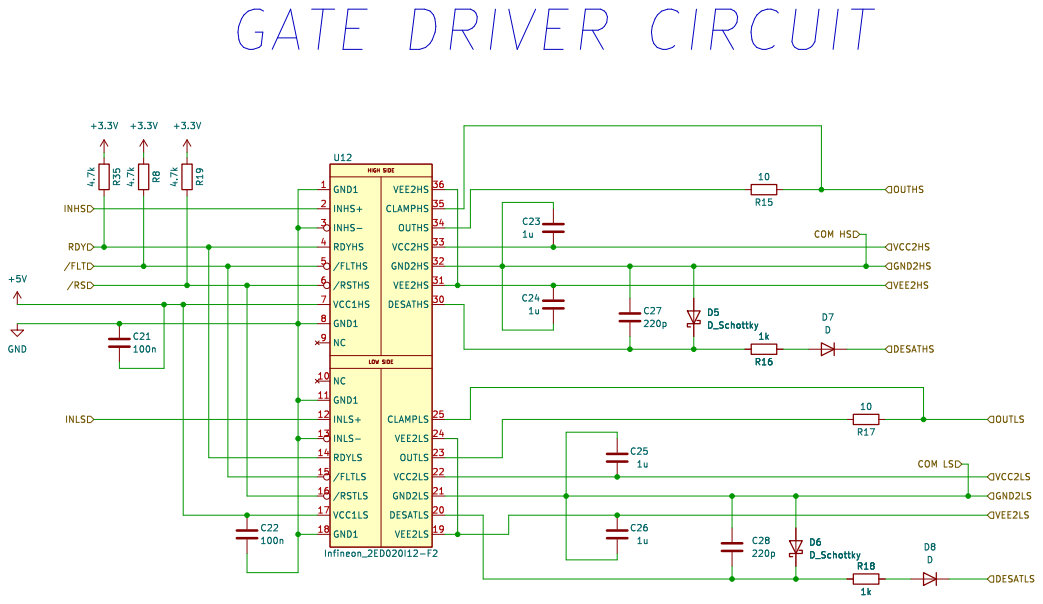
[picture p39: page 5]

VCC2HS OUTHS GATE DRIVER CIRCUIT

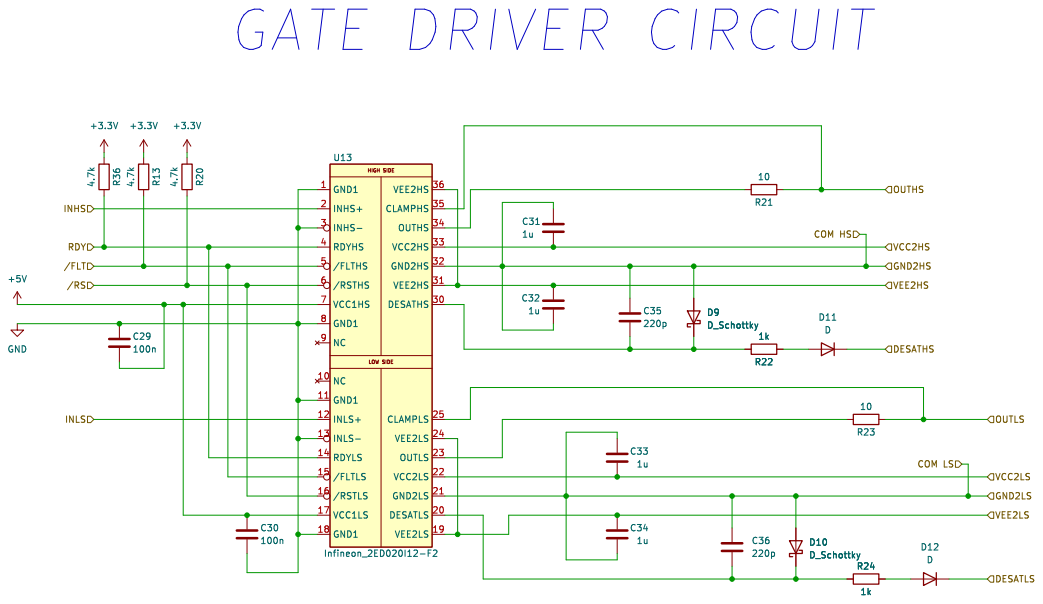
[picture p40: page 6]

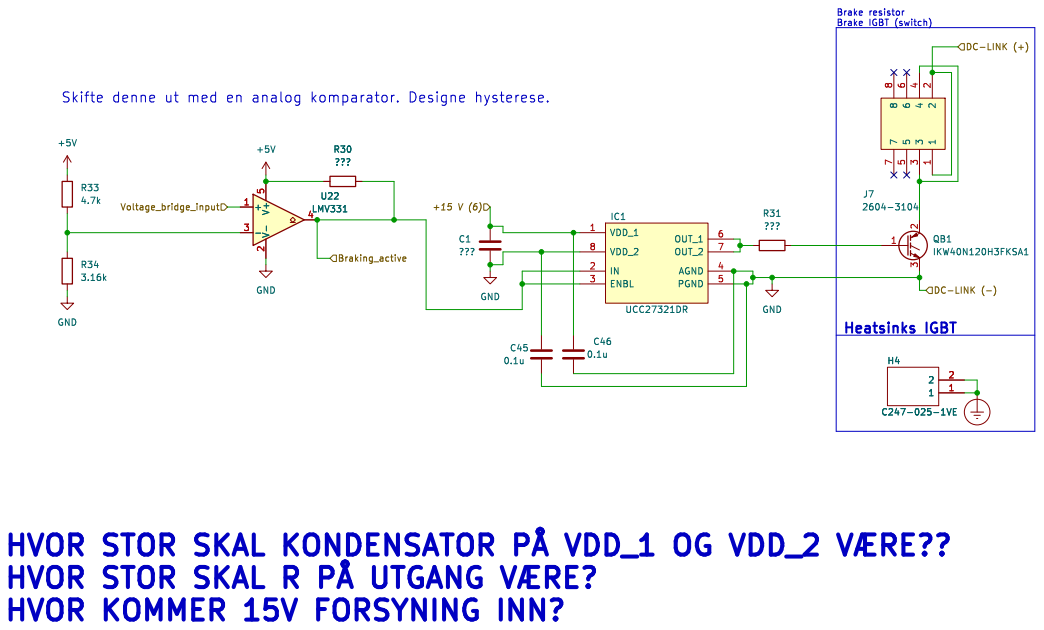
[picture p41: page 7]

File: Braking.kicad_sch Sheet: /Braking/

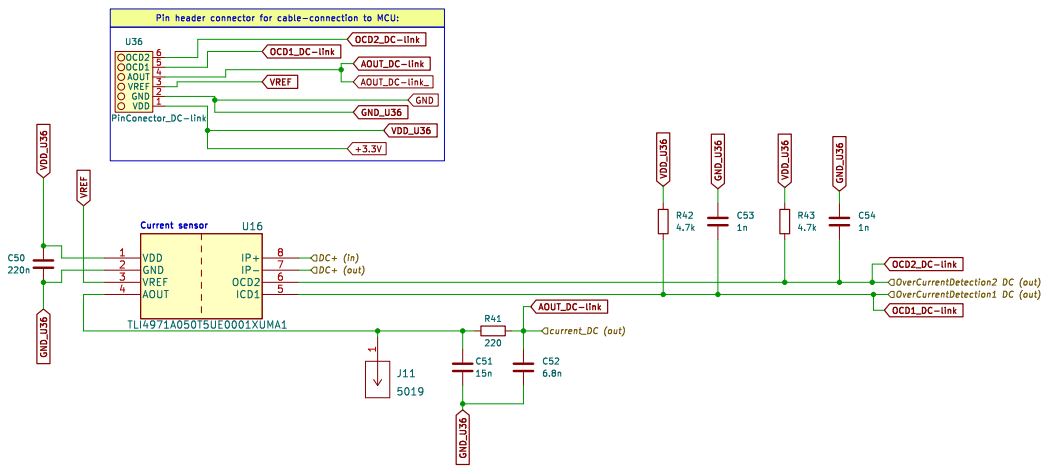
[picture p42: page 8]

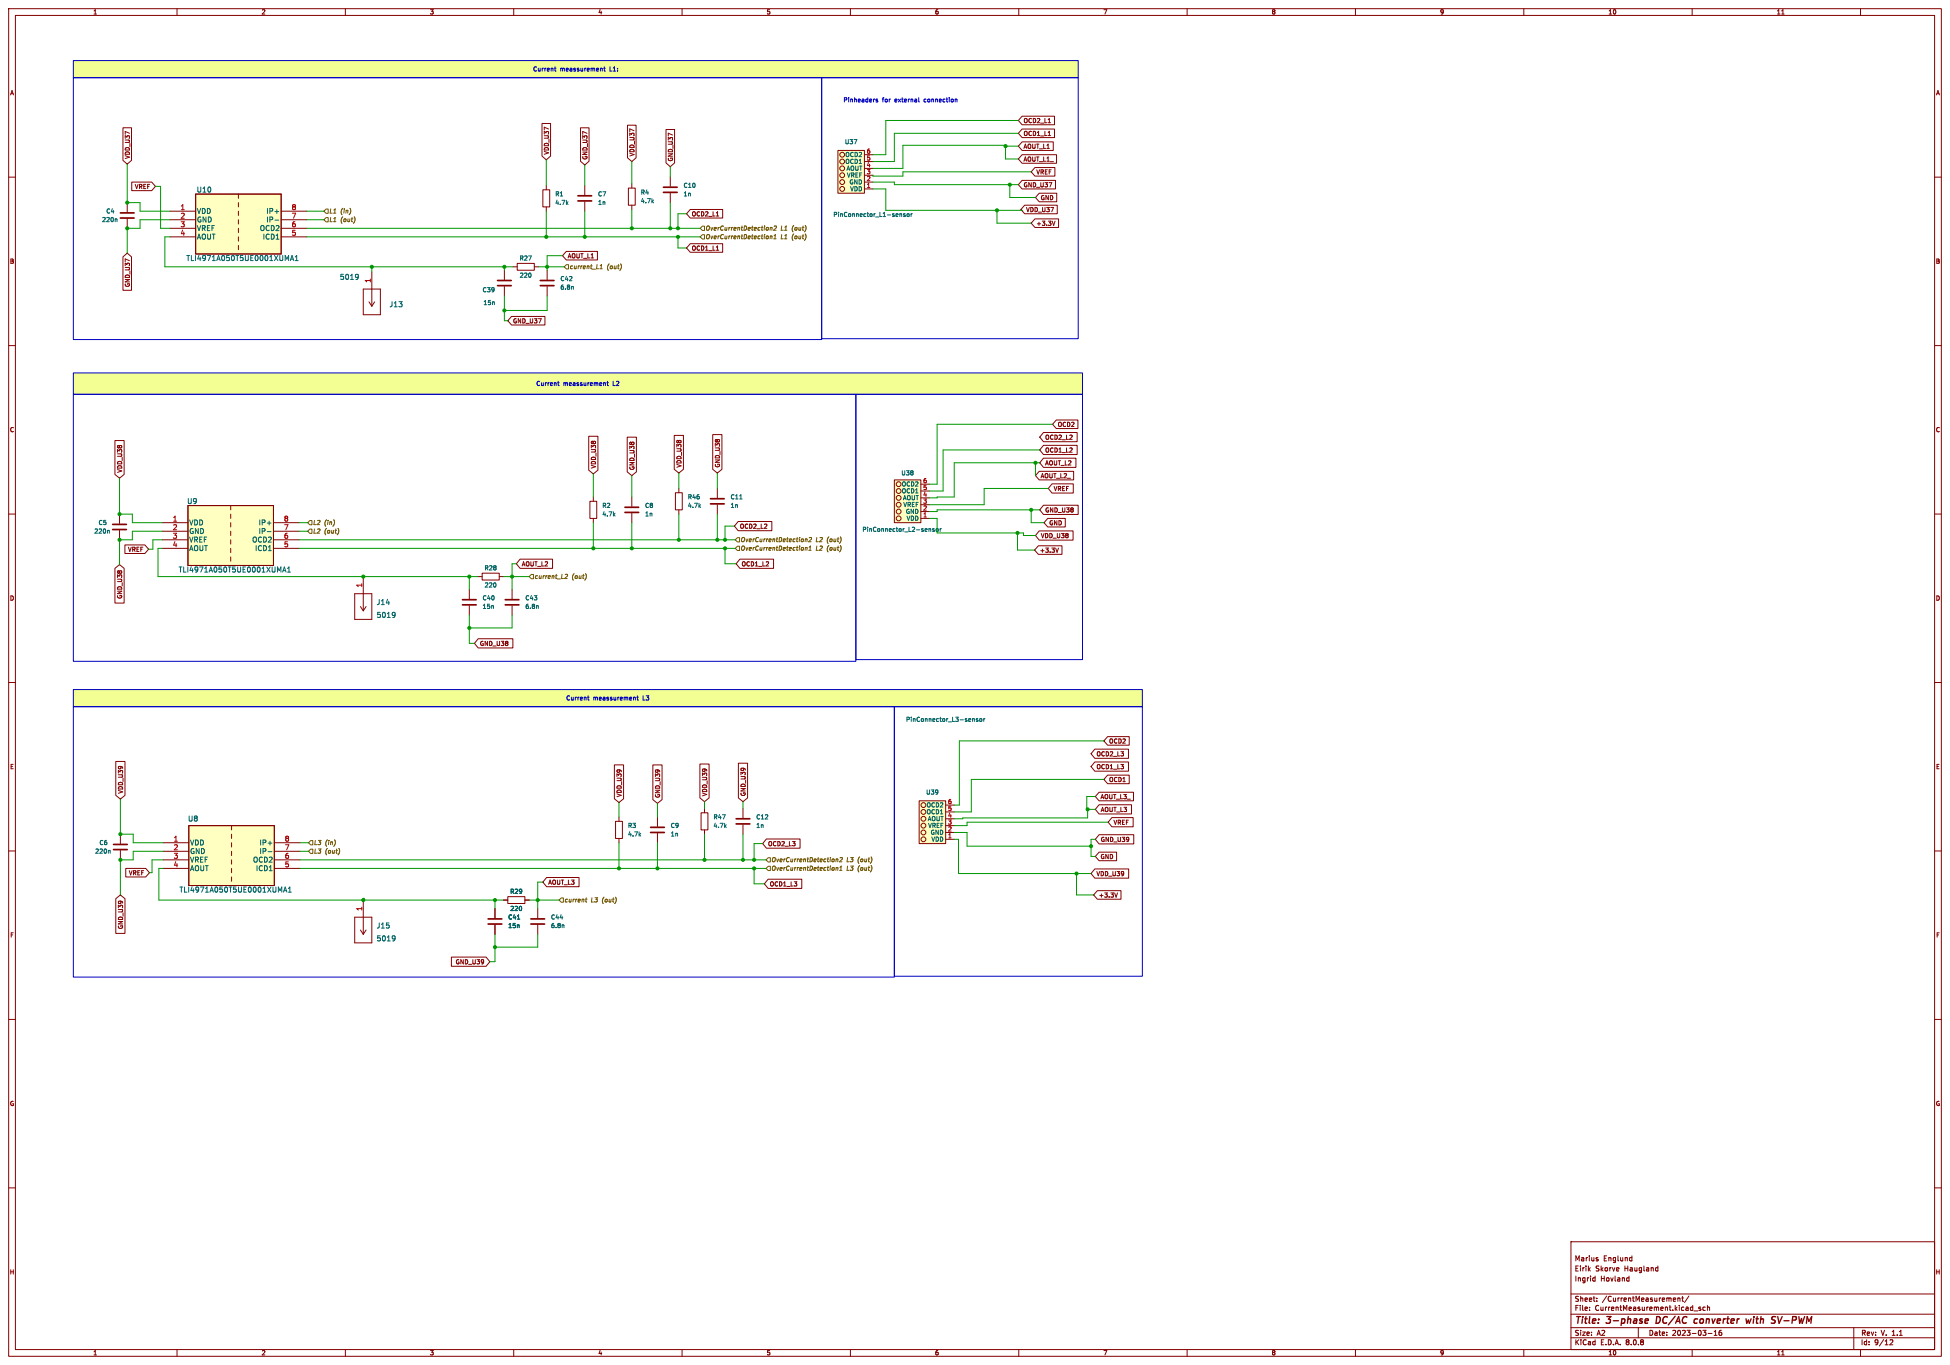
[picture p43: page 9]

File: CurrentMeasurement.kicad_sch Sheet: /CurrentMeasurement/

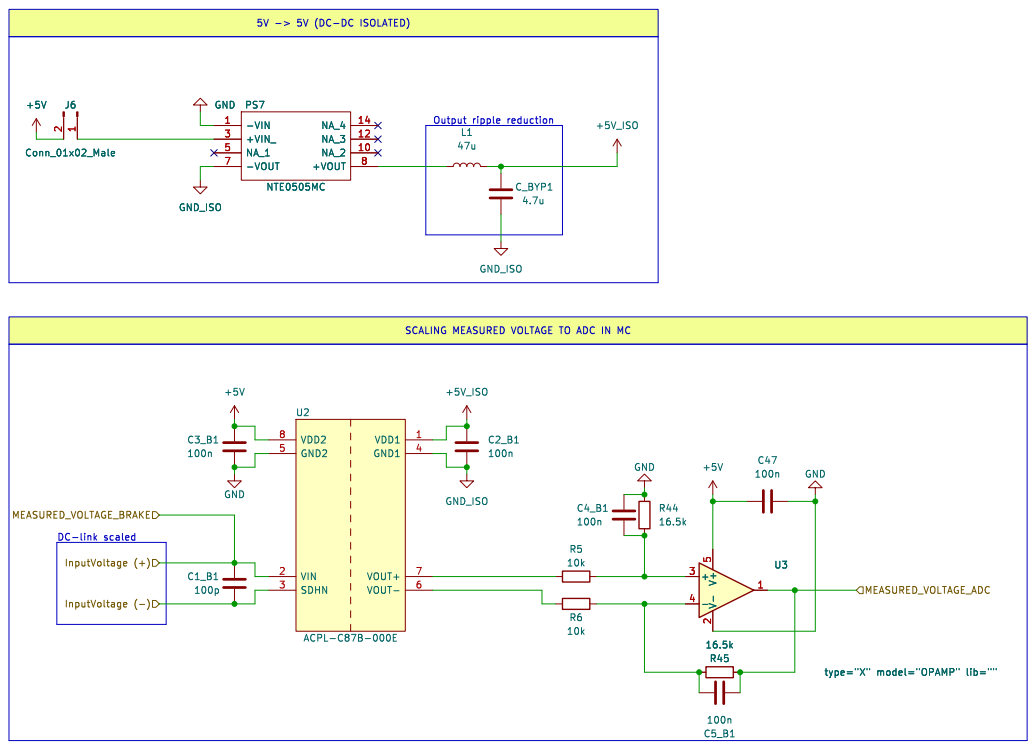
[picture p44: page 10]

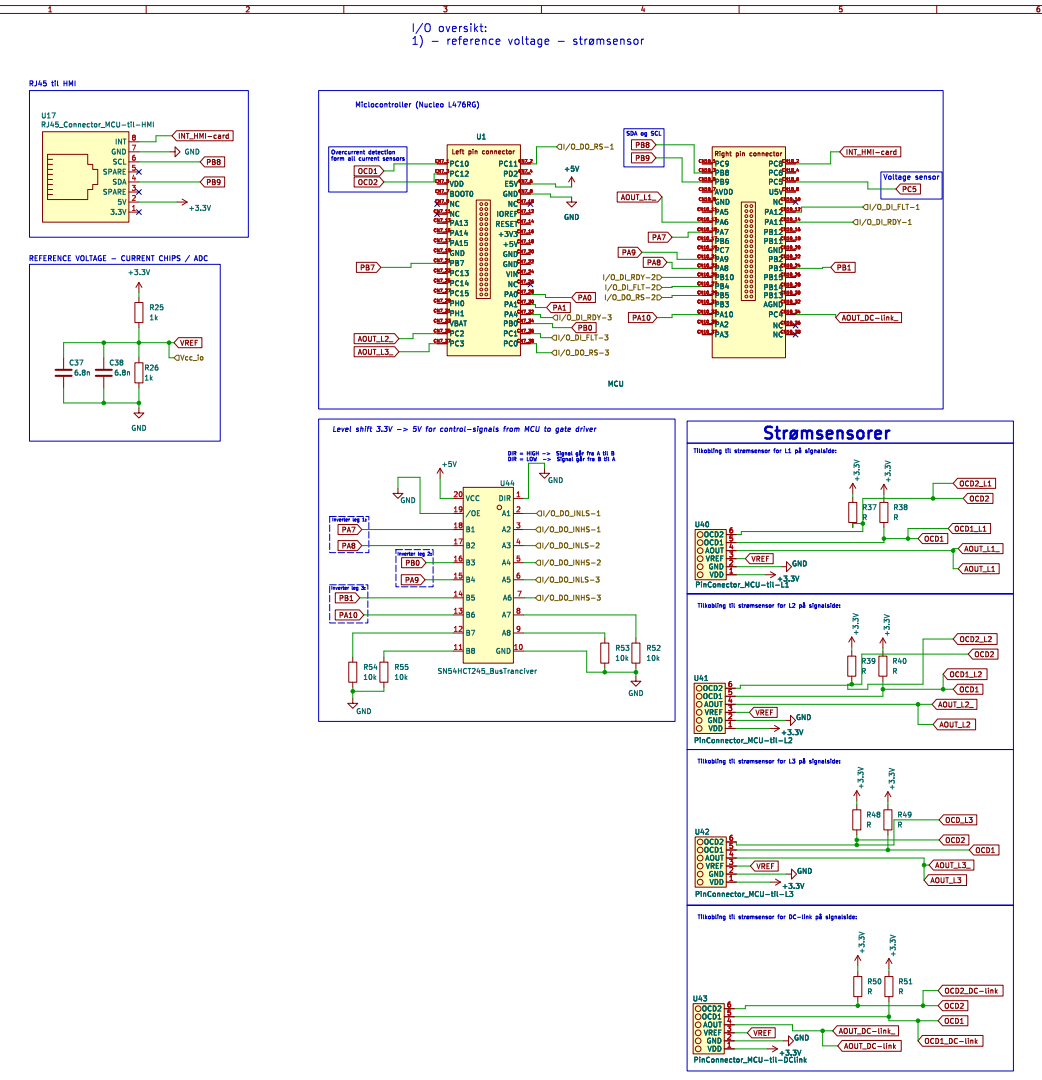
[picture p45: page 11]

5V 2 SPARE 3 SDA 4 SPARE 5 SCL 6 GND 7

File: Microcontroller.kicad_sch Sheet: /Microcontroller/

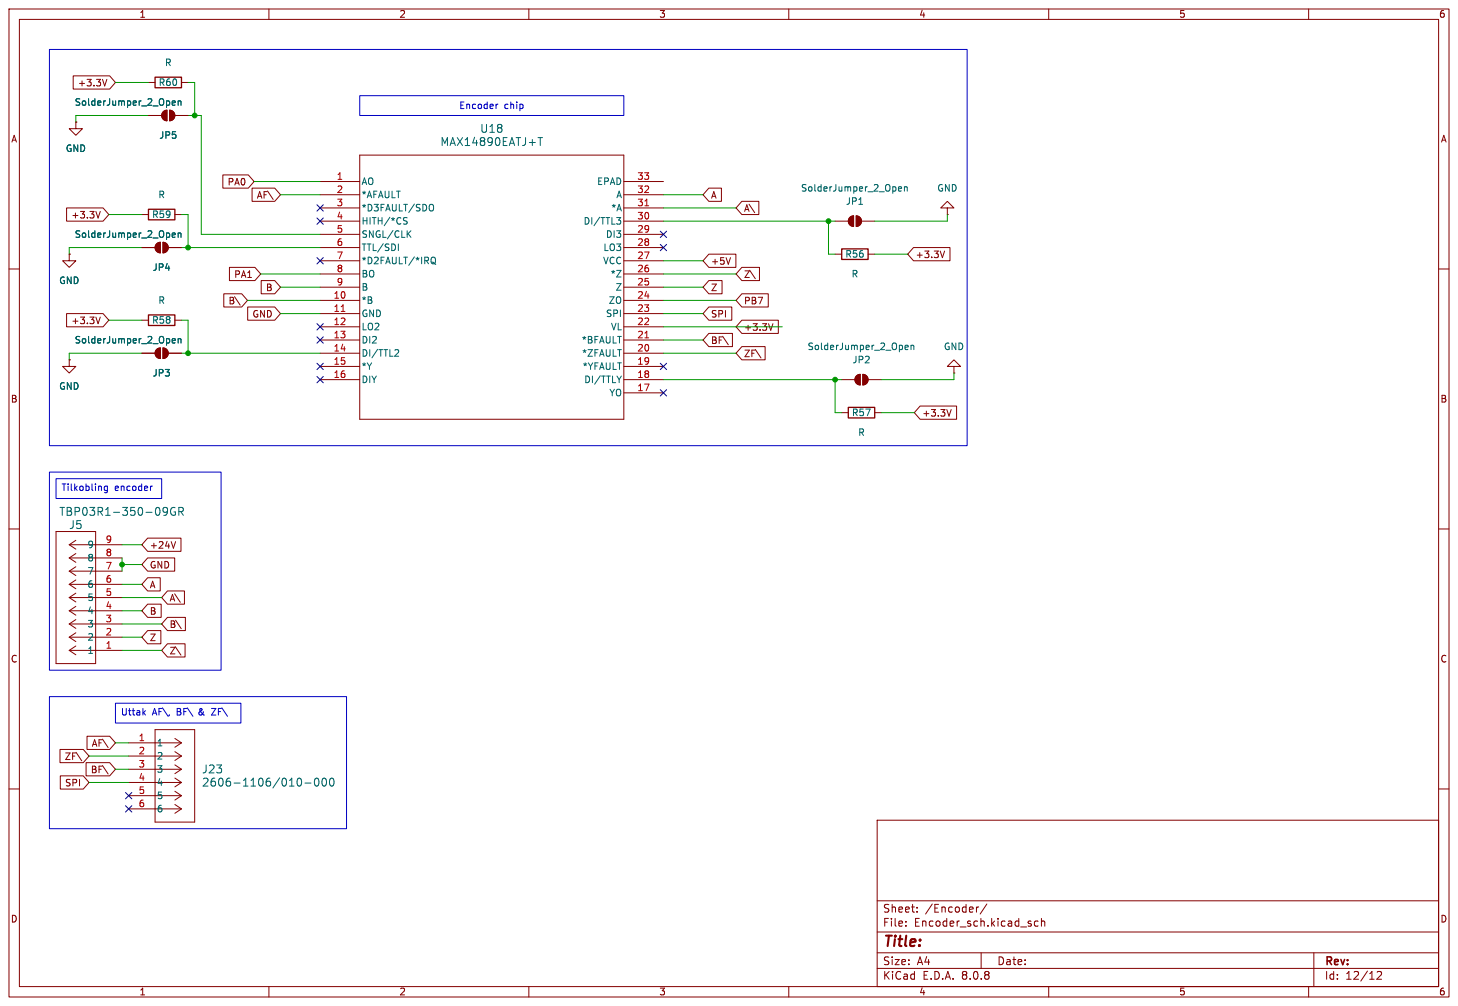
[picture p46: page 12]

Id: 12/12 Title: File: Encoder_sch.kicad_sch Sheet: /Encoder/

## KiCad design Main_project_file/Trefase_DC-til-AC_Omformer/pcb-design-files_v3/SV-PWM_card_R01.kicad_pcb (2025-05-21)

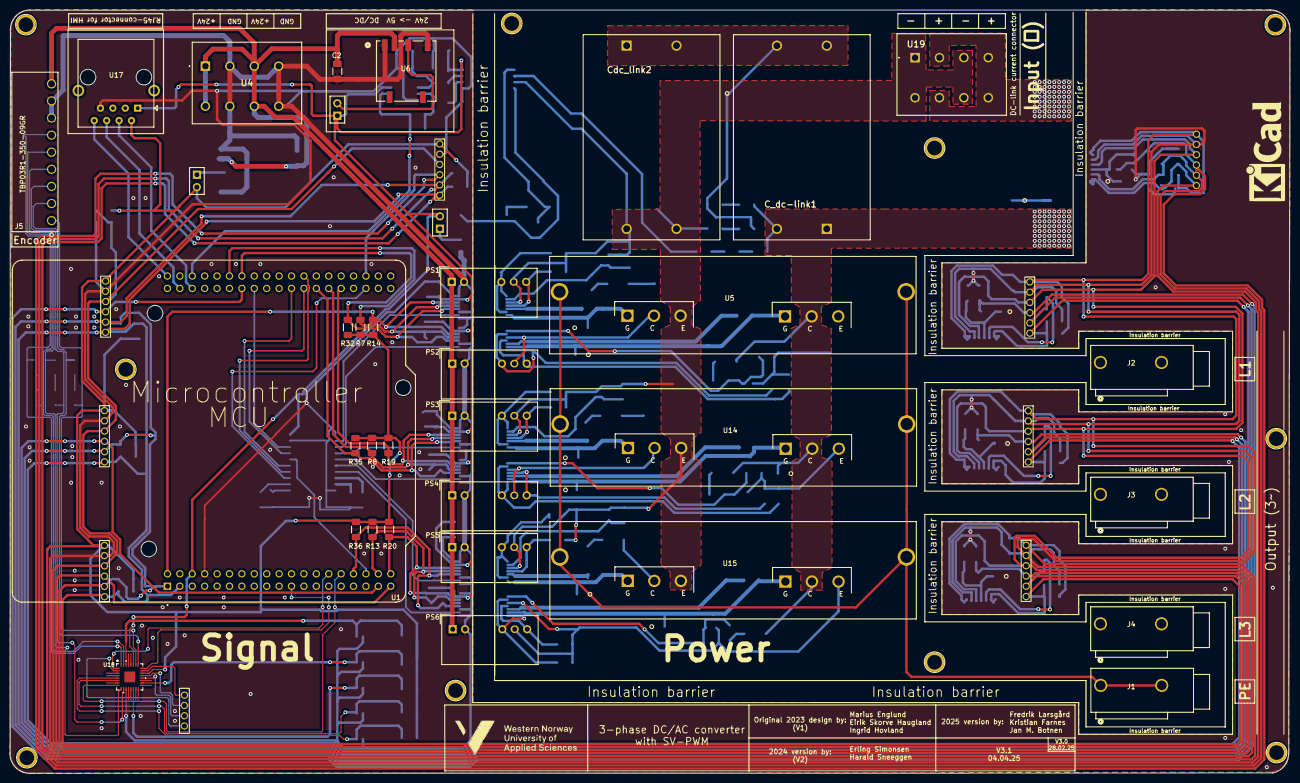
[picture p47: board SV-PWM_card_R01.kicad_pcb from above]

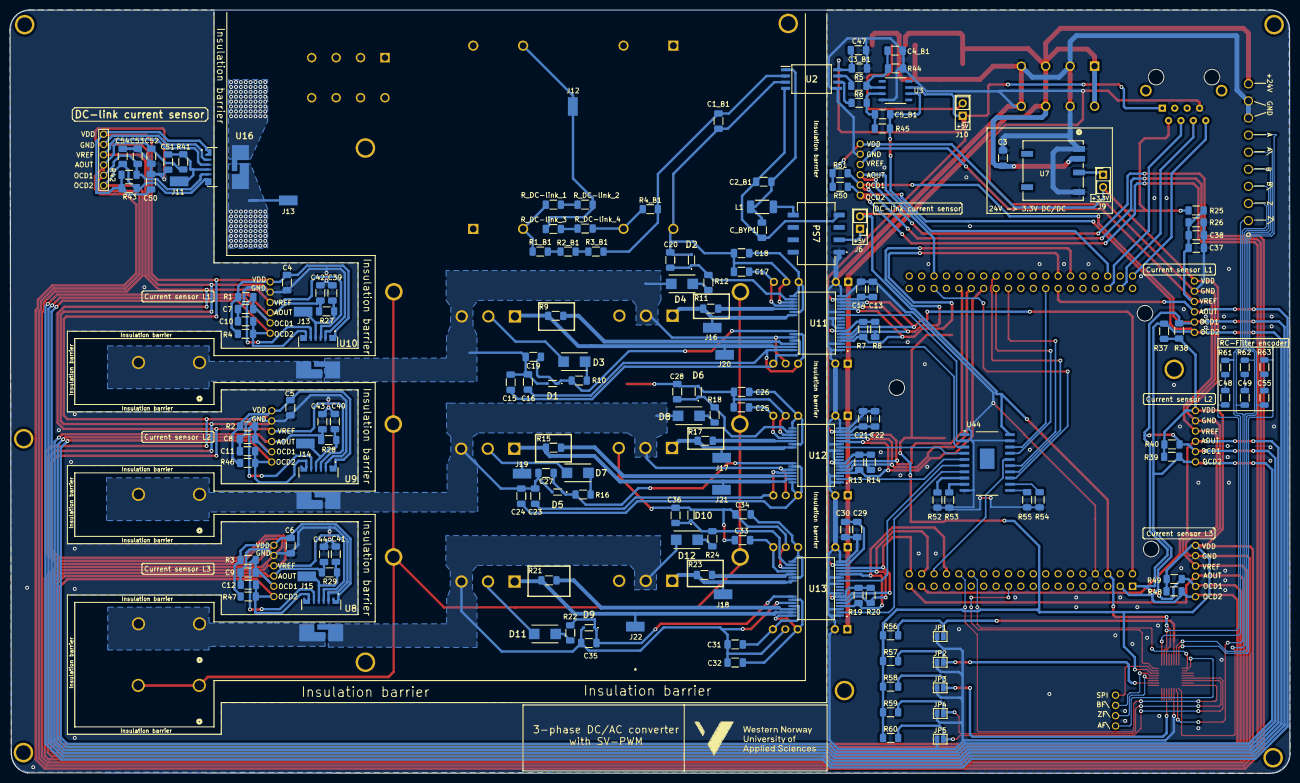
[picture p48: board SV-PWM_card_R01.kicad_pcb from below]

Board: 2 copper layers, 262.0 x 156.2 mm, 218 parts (168 on the bottom side), 126 nets.

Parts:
C1_B1: 100p; C_1206_3216Metric_Pad1.33x1.80mm_HandSolder
C2: 10u; C_1206_3216Metric_Pad1.33x1.80mm_HandSolder
C2_B1, C3_B1, C4_B1, C5_B1, C13, C14, C21, C22, C29, C30, C47: 100n; C_1206_3216Metric_Pad1.33x1.80mm_HandSolder
C3: 22u; C_1206_3216Metric_Pad1.33x1.80mm_HandSolder
C4, C5, C6, C50: 220n; C_1206_3216Metric_Pad1.33x1.80mm_HandSolder
C7, C8, C9, C10, C11, C12, C53, C54: 1n; C_1206_3216Metric_Pad1.33x1.80mm_HandSolder
C15, C16, C17, C18, C23, C24, C25, C26, C31, C32, C33, C34: 1u; C_1206_3216Metric_Pad1.33x1.80mm_HandSolder
C19, C20, C27, C28, C35, C36: 220p; C_1206_3216Metric_Pad1.33x1.80mm_HandSolder
C37, C38, C42, C43, C44, C52: 6.8n; C_1206_3216Metric_Pad1.33x1.80mm_HandSolder
C39, C40, C41, C51: 15n; C_1206_3216Metric_Pad1.33x1.80mm_HandSolder
C48, C49, C55: 100p; C_1206_3216Metric
C_BYP1: 4.7u; C_1206_3216Metric_Pad1.33x1.80mm_HandSolder
C_dc-link1: 14u; DC-link-capacitor-B32776G0146K000
Cdc_link2: 14u; DC-link-capacitor-B32776G0146K000
D1, D2, D5, D6, D9, D10: D_Schottky; Schottky-BAT165AX
D3, D4, D7, D8, D11, D12: D; Diode-SMBJ50CA
H6, H6#2, H6#3, H7, H7#2, H7#3, H7#4, H7#5, H7#6, H8: MountingHole; Skru-hull_3mm
J1, J2, J3, J4: WAGO_2606-1101; CONN_2606-1101_WAG
J5: TBP03R1-350-09GR; TBP03R1-350-03GR
J6, J9, J10: Conn_01x02_Male; PinHeader_1x02_P2.54mm_Vertical
J11, J12, J13, J13#2, J14, J15, J16, J17, J18, J19, J20, J21, J22: 5019; Keystone-5019
J23: 2606-1106/010-000; 6PinHeaderConnector_Strømsensor
JP1, JP2, JP3, JP4, JP5: SolderJumper_2_Open; SolderJumper-2_P1.3mm_Open_Pad1.0x1.5mm
L1: 47u; L_2010_5025Metric_Pad1.52x2.65mm_HandSolder
PS1, PS2, PS3, PS4, PS5, PS6: MGJ2D241509SC; Converter_DCDC_Murata_MGJ2DxxxxxxSC_THT
PS7: NTE0505MC; DC-DC-NTE0505MC
R1, R2, R3, R4, R7, R7#2, R8, R8#2, R13, R13#2, R14, R14#2, R19, R19#2, R20, R20#2, R32, R35, R36, R42, R43, R46, R47: 4.7k; R_1206_3216Metric_Pad1.30x1.75mm_HandSolder
R1_B1, R2_B1, R3_B1: 500k; R_1206_3216Metric_Pad1.30x1.75mm_HandSolder
R4_B1: 3.75k; R_1206_3216Metric_Pad1.30x1.75mm_HandSolder
R5, R6, R52, R53, R54, R55: 10k; R_1206_3216Metric_Pad1.30x1.75mm_HandSolder
R9, R11, R15, R17, R21, R23: 10; R_1206_3216Metric_Pad1.30x1.75mm_HandSolder
R10, R12, R16, R18, R22, R24, R25, R26: 1k; R_1206_3216Metric_Pad1.30x1.75mm_HandSolder
R27, R28, R29, R41: 220; R_1206_3216Metric_Pad1.30x1.75mm_HandSolder
R37, R38, R39, R40, R48, R49, R50, R51, R56, R57, R58, R59, R60: R; R_1206_3216Metric_Pad1.30x1.75mm_HandSolder
R44, R45: 16.5k; R_1206_3216Metric_Pad1.30x1.75mm_HandSolder
R61, R62, R63: 270; R_1206_3216Metric
R_DC-link_1, R_DC-link_2, R_DC-link_3, R_DC-link_4: ???; R_1206_3216Metric_Pad1.30x1.75mm_HandSolder
U1: MCU; MODULE_NUCLEO-L476RG
U2: ACPL-C87B-000E; ACPL-SOIC127P1150X331-8N
U3: type="X" model="OPAMP" lib=""; D8
U4, U19: Wago_2604-3104; WAGO-26043104
U5: Inverter leg nr 1; Inverter leg
U6: MP-K7805T-500R3; TRN 1&slash_3SM_SINGLE_TRP
U7: TRN 1-2410SM; TRN 1&slash_3SM_SINGLE_TRP
U8, U9, U10, U16: TLI4971A050T5UE0001XUMA1
U11, U12, U13: Infineon_2ED020I12-F2; GateDriver-2ED020I12F2XUMA1
U14: Inverter leg nr 2; Inverter leg
U15: Inverter leg nr 3; Inverter leg
U17: RJ45_Connector_MCU-til-HMI; RJ45_Amphenol_54602-x08_Horizontal
U18: MAX14890EATJ+T; 21-0140_T3255&plus_6_MXM_Encoder_chip
U36: PinConector_DC-link; 6PinHeaderConnector_Strømsensor
U37: PinConnector_L1-sensor; 6PinHeaderConnector_Strømsensor
U38: PinConnector_L2-sensor; 6PinHeaderConnector_Strømsensor
U39: PinConnector_L3-sensor; 6PinHeaderConnector_Strømsensor
U40: PinConector_MCU-til-L1; 6PinHeaderConnector_Strømsensor
U41: PinConnector_MCU-til-L2; 6PinHeaderConnector_Strømsensor
U42: PinConnector_MCU-til-L3; 6PinHeaderConnector_Strømsensor
U43: PinConnector_MCU-til-DClink; 6PinHeaderConnector_Strømsensor
U44: SN54HCT245_BusTranciver; ETSSOP-20-1EP_4.4x6.5mm_P0.65mm_EP3x4.2mm_ny123

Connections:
+3.3V: C4.1, C5.1, C6.1, C50.2, J9.1, J9.2, R1.1, R2.1, R3.1, R4.1, R7.1, R8.1, R13.1, R14.1, R19.1, R20.1, R25.1, R32.1, R35.1, R36.1, R37.1, R38.1, R39.1, R40.1, R42.1, R43.1, R46.1, R47.1, R48.1, R49.1, R50.1, R51.1, R56.1, R57.1, R58.1, R59.1, R60.1, U7.3 (NC), U8.1 (VDD), U9.1 (VDD), U10.1 (VDD), U16.1 (VDD), U17.2 (5V), U18.22 (VL), U36.1 (VDD), U37.1 (VDD), U38.1 (VDD), U39.1 (VDD), U40.1 (VDD), U41.1 (VDD), U42.1 (VDD), U43.1 (VDD)
+5V: C3_B1.1, C13.1, C14.2, C21.1, C22.2, C29.1, C30.2, C47.1, J6.2, J10.1, R7#2.2, R8#2.2, R13#2.2, R14#2.2, R19#2.2, R20#2.2, U1.CN7_6 (E5V), U2.8 (VDD2), U3.7, U11.7 (VCC1HS), U11.17 (VCC1LS), U12.7 (VCC1HS), U12.17 (VCC1LS), U13.7 (VCC1HS), U13.17 (VCC1LS), U17.1 (3.3V), U18.27 (VCC), U44.20 (VCC)
+5V_ISO: C2_B1.1, C_BYP1.1, L1.2, U2.1 (VDD1)
+15 V (1): C17.1, PS1.7 (+VOUT), U11.22 (VCC2LS)
+15 V (2): C15.2, PS2.7 (+VOUT), U11.33 (VCC2HS)
+15 V (3): C25.1, PS3.7 (+VOUT), U12.22 (VCC2LS)
+15 V (4): C23.2, PS4.7 (+VOUT), U12.33 (VCC2HS)
+15 V (5): C33.1, PS5.7 (+VOUT), U13.22 (VCC2LS)
+15 V (6): C31.2, PS6.7 (+VOUT), U13.33 (VCC2HS)
+24V: C2.1, C3.1, J5.9, PS1.1 (+VIN), PS2.1 (+VIN), PS3.1 (+VIN), PS4.1 (+VIN), PS5.1 (+VIN), PS6.1 (+VIN), U4.1, U4.2, U4.5, U4.6, U6.2 (+Vin), U7.2 (SENSE)
+DC-link: U16.8 (IP+), U19.3, U19.4, U19.7, U19.8
-8.7 V (1): C18.1, PS1.5 (-VOUT), U11.19 (VEE2LS), U11.24 (VEE2LS)
-8.7 V (2): C16.1, PS2.5 (-VOUT), U11.31 (VEE2HS), U11.36 (VEE2HS)
-8.7 V (3): C26.1, PS3.5 (-VOUT), U12.19 (VEE2LS), U12.24 (VEE2LS)
-8.7 V (4): C24.1, PS4.5 (-VOUT), U12.31 (VEE2HS), U12.36 (VEE2HS)
-8.7 V (5): C34.1, PS5.5 (-VOUT), U13.19 (VEE2LS), U13.24 (VEE2LS)
-8.7 V (6): C32.1, PS6.5 (-VOUT), U13.31 (VEE2HS), U13.36 (VEE2HS)
/CurrentMeasurement/L1 (out): J2.1, J2.2 (1), U10.7 (IP-)
/CurrentMeasurement/L2 (out): J3.1, J3.2 (1), U9.7 (IP-)
/CurrentMeasurement/L3 (out): J4.1, J4.2 (1), U8.7 (IP-)
/GateDriver1/OUTHS: J20.1, R9.1, U5.2 (Gate_HS), U11.35 (CLAMPHS)
/GateDriver1/OUTLS: J16.1, R11.1, U5.5 (Gate_LS), U11.25 (CLAMPLS)
/GateDriver2/OUTHS: J21.1, R15.1, U12.35 (CLAMPHS), U14.2 (Gate_HS)
/GateDriver2/OUTLS: J17.1, R17.1, U12.25 (CLAMPLS), U14.5 (Gate_LS)
/GateDriver3/OUTHS: J22.1, R21.1, U13.35 (CLAMPHS), U15.2 (Gate_HS)
/GateDriver3/OUTLS: J18.1, R23.1, U13.25 (CLAMPLS), U15.5 (Gate_LS)
A: J5.6, R63.1, U18.32 (A)
AF\: J23.1, U18.2 (*AFAULT)
AOUT_DC-link: C52.1, R41.2, U1.CN10_34 (PC4), U36.4 (AOUT), U43.4 (AOUT)
AOUT_L1: C42.1, R27.2, U1.CN10_13 (PA6), U37.4 (AOUT), U40.4 (AOUT)
AOUT_L2: C43.1, R28.2, U1.CN7_35 (PC2), U38.4 (AOUT), U41.4 (AOUT)
AOUT_L3: C44.1, R29.2, U1.CN7_37 (PC3), U39.4 (AOUT), U42.4 (AOUT)
A\: C55.2, J5.5, U18.31 (*A)
B: J5.4, R62.1, U18.9 (B)
BF\: J23.3, U18.21 (*BFAULT)
B\: C49.2, J5.3, U18.10 (*B)
COM (1): C1_B1.2, C17.2, C18.2, C20.2, C25.2, C26.2, C28.2, C33.2, C34.2, C36.2, Cdc_link2.2, Cdc_link2.4, D2.2 (A), D6.2 (A), D10.2 (A), PS1.6 (0V), PS3.6 (0V), PS5.6 (0V), R4_B1.1, R_DC-link_4.2, U2.3 (SDHN), U5.6 (Emitter_LS), U11.21 (GND2LS), U12.21 (GND2LS), U13.21 (GND2LS), U14.6 (Emitter_LS), U15.6 (Emitter_LS), U19.1, U19.2, U19.5, U19.6
COM (2): C15.1, C16.2, C19.2, D1.2 (A), D4.1 (K), PS2.6 (0V), U5.3 (Emitter_HS), U5.4 (Collector_LS), U10.8 (IP+), U11.32 (GND2HS)
COM (4): C23.1, C24.2, C27.2, D5.2 (A), D8.1 (K), PS4.6 (0V), U9.8 (IP+), U12.32 (GND2HS), U14.3 (Emitter_HS), U14.4 (Collector_LS)
COM (6): C31.1, C32.2, C35.2, D9.2 (A), D12.1 (K), PS6.6 (0V), U8.8 (IP+), U13.32 (GND2HS), U15.3 (Emitter_HS), U15.4 (Collector_LS)
C_DC-link: C_dc-link1.2, C_dc-link1.4, Cdc_link2.1, Cdc_link2.3, J12.1, R_DC-link_2.2, R_DC-link_3.1
DC-LINK-VOLTAGE: C1_B1.1, R3_B1.1, R4_B1.2, U2.2 (VIN)
Earth_Protective: J1.1, J1.2 (1), U5.7 (Heatsink_THT1), U5.8 (Heatsink_THT2), U14.7 (Heatsink_THT1), U14.8 (Heatsink_THT2), U15.7 (Heatsink_THT1), U15.8 (Heatsink_THT2)
GND: C2.2, C3.2, C3_B1.2, C4.2, C4_B1.2, C5.2, C6.2, C7.1, C8.1, C9.1, C10.1, C11.1, C12.1, C13.2, C14.1, C21.2, C22.1, C29.2, C30.1, C37.2, C38.2, C39.2, C40.2, C41.2, C42.2, C43.2, C44.2, C47.2, C50.1, C51.2, C52.2, C53.1, C54.1, J5.7, J5.8, JP1.1 (A), JP2.1 (A), JP3.1 (A), JP4.1 (A), JP5.1 (A), PS1.2 (-VIN), PS2.2 (-VIN), PS3.2 (-VIN), PS4.2 (-VIN), PS5.2 (-VIN), PS6.2 (-VIN), PS7.1 (-VIN), R26.2, R44.2, R52.2, R53.2, R54.2, R55.2, U1.CN7_8 (GND), U2.5 (GND2), U3.4 (-), U4.3, U4.4, U4.7, U4.8, U6.1 (+Vin), U6.5 (+Vout), U7.1 (Q), U7.5 (EN), U8.2 (GND), U9.2 (GND), U10.2 (GND), U11.1 (GND1), U11.3 (INHS-), U11.8 (GND1), U11.11 (GND1), U11.13 (INLS-), U11.18 (GND1), U12.1 (GND1), U12.3 (INHS-), U12.8 (GND1), U12.11 (GND1), U12.13 (INLS-), U12.18 (GND1), U13.1 (GND1), U13.3 (INHS-), U13.8 (GND1), U13.11 (GND1), U13.13 (INLS-), U13.18 (GND1), U16.2 (GND), U17.7 (GND), U18.11 (GND), U36.2 (GND), U37.2 (GND), U38.2 (GND), U39.2 (GND), U40.2 (GND), U41.2 (GND), U42.2 (GND), U43.2 (GND), U44.1 (DIR), U44.10 (GND), U44.19 (/OE)
GND_ISO: C2_B1.2, C_BYP1.2, PS7.7 (-VOUT), U2.4 (GND1)
INT_HMI-card: U1.CN10_2 (PC8), U17.8 (INT)
I/O_DI_FLT-1: R7.2, R8#2.1, U1.CN10_12 (PA12), U11.5 (/FLTHS), U11.15 (/FLTLS)
I/O_DI_FLT-2: R8.2, R14#2.1, U1.CN10_27 (PB4), U12.5 (/FLTHS), U12.15 (/FLTLS)
I/O_DI_FLT-3: R13.2, R20#2.1, U1.CN7_36 (PC1), U13.5 (/FLTHS), U13.15 (/FLTLS)
I/O_DI_RDY-1: R7#2.1, R32.2, U1.CN10_14 (PA11), U11.4 (RDYHS), U11.14 (RDYLS)
I/O_DI_RDY-2: R13#2.1, R35.2, U1.CN10_25 (PB10), U12.4 (RDYHS), U12.14 (RDYLS)
I/O_DI_RDY-3: R19#2.1, R36.2, U1.CN7_32 (PA4), U13.4 (RDYHS), U13.14 (RDYLS)
I/O_DO_INHS-1: U11.2 (INHS+), U44.3 (A2)
I/O_DO_INHS-2: U12.2 (INHS+), U44.5 (A4)
I/O_DO_INHS-3: U13.2 (INHS+), U44.7 (A6)
I/O_DO_INLS-1: U11.12 (INLS+), U44.2 (A1)
I/O_DO_INLS-2: U12.12 (INLS+), U44.4 (A3)
I/O_DO_INLS-3: U13.12 (INLS+), U44.6 (A5)
I/O_DO_RS-1: R14.2, U1.CN7_2 (PC11), U11.6 (/RSTHS), U11.16 (/RSTLS)
I/O_DO_RS-2: R19.2, U1.CN10_29 (PB5), U12.6 (/RSTHS), U12.16 (/RSTLS)
I/O_DO_RS-3: R20.2, U1.CN7_38 (PC0), U13.6 (/RSTHS), U13.16 (/RSTLS)
unnamed: C48.1, R61.2
unnamed: C49.1, R62.2
unnamed: C55.1, R63.2
unnamed: C19.1, D1.1 (K), R10.2, U11.30 (DESATHS)
unnamed: C20.1, D2.1 (K), R12.2, U11.20 (DESATLS)
unnamed: D3.2 (A), R10.1
unnamed: D4.2 (A), R12.1
unnamed: C27.1, D5.1 (K), R16.2, U12.30 (DESATHS)
unnamed: C28.1, D6.1 (K), R18.2, U12.20 (DESATLS)
unnamed: D7.2 (A), R16.1
unnamed: D8.2 (A), R18.1
unnamed: C35.1, D9.1 (K), R22.2, U13.30 (DESATHS)
unnamed: C36.1, D10.1 (K), R24.2, U13.20 (DESATLS)
unnamed: D11.2 (A), R22.1
unnamed: D12.2 (A), R24.1
unnamed: J6.1, PS7.3 (+VIN_)
unnamed: J10.2, U6.3 (GND)
unnamed: JP1.2 (B), R56.2, U18.30 (DI/TTL3)
unnamed: JP2.2 (B), R57.2, U18.18 (DI/TTLY)
unnamed: JP3.2 (B), R58.2, U18.14 (DI/TTL2)
unnamed: JP4.2 (B), R59.2, U18.6 (TTL/SDI)
unnamed: JP5.2 (B), R60.2, U18.5 (SNGL/CLK)
unnamed: L1.1, PS7.8 (+VOUT)
unnamed: R1_B1.2, R2_B1.1
unnamed: R2_B1.2, R3_B1.2
unnamed: R_DC-link_1.2, R_DC-link_2.1
unnamed: R_DC-link_3.2, R_DC-link_4.1
unnamed: R5.1, U2.7 (VOUT+)
unnamed: R6.1, U2.6 (VOUT-)
unnamed: C4_B1.1, R5.2, R44.1, U3.2 (V-)
unnamed: C5_B1.2, R6.2, R45.2, U3.3 (+)
unnamed: C41.1, J15.1, R29.1, U8.4 (AOUT)
unnamed: C40.1, J14.1, R28.1, U9.4 (AOUT)
unnamed: C39.1, J13#2.1, R27.1, U10.4 (AOUT)
unnamed: R9.2, U11.34 (OUTHS)
unnamed: R11.2, U11.23 (OUTLS)
unnamed: R15.2, U12.34 (OUTHS)
unnamed: R17.2, U12.23 (OUTLS)
unnamed: R21.2, U13.34 (OUTHS)
unnamed: R23.2, U13.23 (OUTLS)
unnamed: C51.1, J11.1, R41.1, U16.4 (AOUT)
unnamed: R52.1, U44.8 (A7)
unnamed: R53.1, U44.9 (A8)
unnamed: R54.1, U44.12 (B7)
unnamed: R55.1, U44.11 (B8)
OCD1: C7.2, C8.2, C9.2, C53.2, R1.2, R2.2, R3.2, R38.2, R40.2, R42.2, R49.2, R51.2, U1.CN7_1 (PC10), U8.5 (ICD1), U9.5 (ICD1), U10.5 (ICD1), U16.5 (ICD1), U36.5 (OCD1), U37.5 (OCD1), U38.5 (OCD1), U39.5 (OCD1), U40.5 (OCD1), U41.5 (OCD1), U42.5 (OCD1), U43.5 (OCD1)
OCD2: C10.2, C11.2, C12.2, C54.2, R4.2, R37.2, R39.2, R43.2, R46.2, R47.2, R48.2, R50.2, U1.CN7_3 (PC12), U8.6 (OCD2), U9.6 (OCD2), U10.6 (OCD2), U16.6 (OCD2), U36.6 (OCD2), U37.6 (OCD2), U38.6 (OCD2), U39.6 (OCD2), U40.6 (OCD2), U41.6 (OCD2), U42.6 (OCD2), U43.6 (OCD2)
PA0: U1.CN7_28 (PA0), U18.1 (AO)
PA1: U1.CN7_30 (PA1), U18.8 (BO)
PA7: U1.CN10_15 (PA7), U44.18 (B1)
PA8: U1.CN10_23 (PA8), U44.17 (B2)
PA9: U1.CN10_21 (PA9), U44.15 (B4)
PA10: U1.CN10_33 (PA10), U44.13 (B6)
PB0: U1.CN7_34 (PB0), U44.16 (B3)
PB1: U1.CN10_24 (PB1), U44.14 (B5)
PB7: U1.CN7_21 (PB7), U18.24 (ZO)
PB8: U1.CN10_3 (PB8), U17.6 (SCL)
PB9: U1.CN10_5 (PB9), U17.4 (SDA)
PC5: C5_B1.1, R45.1, U1.CN10_6 (PC5), U3.6
SPI: J23.4, U18.23 (SPI)
TA+1_HS: C_dc-link1.1, C_dc-link1.3, D3.1 (K), D7.1 (K), D11.1 (K), J13.1, J19.1, R1_B1.1, R_DC-link_1.1, U5.1 (Collector_HS), U14.1 (Collector_HS), U15.1 (Collector_HS), U16.7 (IP-)
VREF: C37.1, C38.1, R25.2, R26.1, U8.3 (VREF), U9.3 (VREF), U10.3 (VREF), U16.3 (VREF), U36.3 (VREF), U37.3 (VREF), U38.3 (VREF), U39.3 (VREF), U40.3 (VREF), U41.3 (VREF), U42.3 (VREF), U43.3 (VREF)
Z: J5.2, R61.1, U18.25 (Z)
ZF\: J23.2, U18.20 (*ZFAULT)
Z\: C48.2, J5.1, U18.26 (*Z)

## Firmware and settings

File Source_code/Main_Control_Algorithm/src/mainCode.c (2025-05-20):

#include <math.h>
#include <stdbool.h>
#include <stm32l4xx_ll_gpio.h>
#include <stm32l4xx_ll_cortex.h>
#include <stm32l4xx_ll_rcc.h>
#include <stm32l4xx_ll_bus.h>
#include <stm32l4xx_ll_tim.h>
#include <stm32l4xx_ll_utils.h>
#include <stm32l4xx_ll_pwr.h>
#include <stm32l4xx_ll_system.h>
#include <stm32l4xx_ll_usart.h>


//_______________________________________________________________________________________________________________________
// Declarations of I/O:


// UART:

#define UART2_PORT            GPIOA             // UART2 Port
#define UART2_TX_PIN          LL_GPIO_PIN_2     // UART2 Transmitter Pin
#define UART2_RX_PIN          LL_GPIO_PIN_3     // UART2 Receiver Pin

// Bulit-in LED:
#define ONBOARD_LED_PORT      GPIOA
#define ONBOARD_LED_PIN       LL_GPIO_PIN_5

// Encoder SW-pin (D10 (Arduino pin) = PB6)
#define SW_PORT               GPIOB
#define SW_PIN                LL_GPIO_PIN_6  

// Direction button (PB14)
#define DIR_Button_PORT       GPIOB
#define DIR_Button_PIN        LL_GPIO_PIN_14
/*
// ON/OFF-button (PB13) 
#define ON_OFF_Button_PORT    GPIOB
#define ON_OFF_Button_PIN     LL_GPIO_PIN_13 */
#define ON_OFF_Button_PORT    GPIOC
#define ON_OFF_Button_PIN     LL_GPIO_PIN_13 //Blå intern knapp for å skru av og på

// Status LEDs:
#define RED_LED_PORT          GPIOB
#define RED_LED_PIN           LL_GPIO_PIN_15
#define GREEN_LED_PORT        GPIOB
#define GREEN_LED_PIN         LL_GPIO_PIN_11
#define YELLOW_LED_PORT       GPIOB
#define YELLOW_LED_PIN        LL_GPIO_PIN_12

/* Gate Driver 1 */
#define DRIVER1_RDY_PORT      GPIOA             // Gate Driver Leg A Ready Port
#define DRIVER1_RDY_PIN       LL_GPIO_PIN_11     // Gate Driver Leg A Ready Pin
#define DRIVER1_INHS_PORT     GPIOA             // Gate Driver Leg A High Side PWM Port
#define DRIVER1_INHS_PIN      LL_GPIO_PIN_8     // Gate Driver Leg A High Side PWM Pin
#define DRIVER1_INLS_PORT     GPIOA             // Gate Driver Leg A Low Side PWM Port
#define DRIVER1_INLS_PIN      LL_GPIO_PIN_7     // Gate Driver Leg A Low Side PWM Pin

#define DRIVER1_RST_PORT      GPIOC             // Gate Driver Leg A Reset Port
#define DRIVER1_RST_PIN       LL_GPIO_PIN_11     // Gate Driver Leg A Reset Pin
#define DRIVER1_FLT_PORT      GPIOA             // Gate Driver Leg A Fault Port
#define DRIVER1_FLT_PIN       LL_GPIO_PIN_12     // Gate Driver Leg A Fault Pin



/* Gate Driver 2 */
#define DRIVER2_RDY_PORT      GPIOB             // Gate Driver Leg B Ready Port
#define DRIVER2_RDY_PIN       LL_GPIO_PIN_10    // Gate Driver Leg B Ready Pin
#define DRIVER2_INHS_PORT     GPIOA             // Gate Driver Leg B High Side PWM Port
#define DRIVER2_INHS_PIN      LL_GPIO_PIN_9     // Gate Driver Leg B High Side PWM Pin
#define DRIVER2_INLS_PORT     GPIOB             // Gate Driver Leg B Low Side PWM Port
#define DRIVER2_INLS_PIN      LL_GPIO_PIN_0     // Gate Driver Leg B Low Side PWM Pin
#define DRIVER2_RST_PORT      GPIOB             // Gate Driver Leg B Reset Port
#define DRIVER2_RST_PIN       LL_GPIO_PIN_5     // Gate Driver Leg B Reset Pin
#define DRIVER2_FLT_PORT      GPIOB             // Gate Driver Leg B Fault Port
#define DRIVER2_FLT_PIN       LL_GPIO_PIN_4     // Gate Driver Leg B Fault Pin

/* Gate Driver 3 */
#define DRIVER3_RDY_PORT      GPIOA             // Gate Driver Leg C Ready Port
#define DRIVER3_RDY_PIN       LL_GPIO_PIN_4     // Gate Driver Leg C Ready Pin
#define DRIVER3_INHS_PORT     GPIOA             // Gate Driver Leg C High Side PWM Port
#define DRIVER3_INHS_PIN      LL_GPIO_PIN_10    // Gate Driver Leg C High Side PWM Pin
#define DRIVER3_INLS_PORT     GPIOB             // Gate Driver Leg C Low Side PWM Port
#define DRIVER3_INLS_PIN      LL_GPIO_PIN_1     // Gate Driver Leg C Low Side PWM Pin
#define DRIVER3_RST_PORT      GPIOC             // Gate Driver Leg C Reset Port
#define DRIVER3_RST_PIN       LL_GPIO_PIN_0     // Gate Driver Leg C Reset Pin
#define DRIVER3_FLT_PORT      GPIOC             // Gate Driver Leg C Fault Port
#define DRIVER3_FLT_PIN       LL_GPIO_PIN_1     // Gate Driver Leg C Fault Pin

/*Trigger for oscilloskop*/

#define TRIGGER_SIGNAL_PWM_PORT GPIOB
#define TRIGGER_SIGNAL_PWM_PIN  LL_GPIO_PIN_8




//_______________________________________________________________________________________________________________________
// Global variables:

uint32_t sine_res_g           = 0;              // No. of Compare Values for Each Period (max 1024).
float sine_table[] = {0,0.0627905195293134,0.125333233564304,0.187381314585725,0.248689887164855,0.309016994374947,0.368124552684678,0.425779291565073,0.481753674101715,0.535826794978997,0.587785252292473,0.63742398974869,0.684547105928689,0.728968627421412,0.770513242775789,0.809016994374947,0.844327925502015,0.876306680043864,0.904827052466019,0.929776485888251,0.951056516295154,0.968583161128631,0.982287250728689,0.992114701314478,0.998026728428272,1,0.998026728428272,0.992114701314478,0.982287250728689,0.968583161128631,0.951056516295154,0.929776485888251,0.904827052466019,0.876306680043864,0.844327925502015,0.809016994374947,0.770513242775789,0.728968627421412,0.684547105928689,0.63742398974869,0.587785252292473,0.535826794978997,0.481753674101715,0.425779291565072,0.368124552684678,0.309016994374947,0.248689887164855,0.187381314585725,0.125333233564304,0.0627905195293133,0,-0.0627905195293133,-0.125333233564304,-0.187381314585725,-0.248689887164855,-0.309016994374947,-0.368124552684678,-0.425779291565072,-0.481753674101715,-0.535826794978997,-0.587785252292473,-0.63742398974869,-0.684547105928689,-0.728968627421412,-0.770513242775789,-0.809016994374947,-0.844327925502015,-0.876306680043863,-0.90482705246602,-0.929776485888251,-0.951056516295154,-0.968583161128631,-0.982287250728689,-0.992114701314478,-0.998026728428272,-1,-0.998026728428272,-0.992114701314478,-0.982287250728689,-0.968583161128631,-0.951056516295154,-0.929776485888251,-0.90482705246602,-0.876306680043863,-0.844327925502015,-0.809016994374947,-0.770513242775789,-0.728968627421412,-0.684547105928689,-0.63742398974869,-0.587785252292473,-0.535826794978996,-0.481753674101715,-0.425779291565072,-0.368124552684678,-0.309016994374947,-0.248689887164854,-0.187381314585725,-0.125333233564304,-0.0627905195293138,0};

uint32_t      modulationFrequency = 0;               // Modulasjonsfrekvens
float         m_a                 = 0;               // Amplitudemodulasjonsindeks
uint32_t      sine_res            = 101;             // Antall verdier i sine_table
float         Vd                  = 0;
uint32_t      interrutCounterLim  = 0;     
bool          on_off              = false;           // Hvis true -> omformer er på , hvis false -> omformer er av (TIM1 teller ikke)          

// Defines valid modulation schemes for the inverter.
typedef enum {
  SPWM = 0,
  SVPWM
} scheme_t;

// Defines valid rotation directions for the rotor.
typedef enum {
  CW = 0,
  CCW
} direction_t;


// Defines valid operating states for the inverter.
typedef enum {
  NOT_READY = 0,
  READY,
  RUNNING,
  FAULT
} state_t;

typedef struct {
  uint32_t L1;
  uint32_t L2;
  uint32_t L3;
} compare_t;

direction_t  direction_g         = CW;               // Rotor Rotation Direction
scheme_t     algorithm_g          = SVPWM;           // Modulation Scheme

//_______________________________________________________________________________________________________________________
// SysTick handler:
void SysTick_Handler(void){

  static uint_fast32_t cnt = 0;
  cnt++;

  if ((cnt % 500) == 0){
   // LL_GPIO_TogglePin(ONBOARD_LED_PORT, ONBOARD_LED_PIN);
  }
}

//_______________________________________________________________________________________________________________________

// Initialize functions:
void enable_gpio_ports_clock();

void initialize_UART();
void initialize_SystemClock();
void initialize_IO();
void initialize_TIM1();
void initialize_TIM2();
void initialize_EncoderTimer();

void generate_SquareWave();

void update_TIM1_compareValue_SPWM_v1(float, uint32_t, uint32_t);
void update_TIM1_compareValue_SPWM_v2(float, uint32_t, uint32_t);
void update_TIM1_compareVale_SVPWM(float, float, uint32_t, uint32_t);

void set_ModulationFrequency_Manually(uint32_t);
void set_SwitchingFrequency_Manually(uint32_t);

uint32_t calculate_MaximunFrequency_SPWM(double, double, double);
double   calculate_AmplitudeModulationIndex(uint32_t, double, double, double);
uint32_t get_encoder_timer_count();

void     read_DirectionButton(void);
void     read_OnOffButton(void);

// Parametre for PWM-algoritmer:
void        set_ModulationFrequency(uint32_t f)
{
  modulationFrequency = f;
}
uint32_t    get_ModulationFrequency(void)
{
  return modulationFrequency;
}
void        set_ModulationAlgorithm(scheme_t algorithm) {

  algorithm_g = algorithm;
}
scheme_t    get_ModulationAlgorithm(void) {

  return algorithm_g;
}
void        set_AmplitudeModulationIndex(float ma)
{
  m_a = ma;
}
float       get_AmplitudeModulationIndex(void)
{
  return m_a;
}
void        set_Vd(float Ud)
{
  Vd = Ud;
}
float       get_Vd(void)
{
  return Vd;
}
void        set_InterruptCounterLimit(uint32_t f)
{
  // Denne funksjonen er dimensjonert for å virke med en klokkefrekvens på 10MHz 
  // med en AutoReload på 100. 

  long     f_tick    = SystemCoreClock / LL_TIM_GetPrescaler(TIM2);
  double   T_tick    = 1 / (double)f_tick;

  double   T_int     = T_tick * LL_TIM_GetAutoReload(TIM2);

  uint32_t f_count     = 101 * f;
  double   T_count     = 1 / (double)f_count;

  uint32_t lim       = (uint32_t)round(T_count / T_int);
  interrutCounterLim = lim;
}
uint32_t    get_InterruptCounterLimit(void)
{
  return interrutCounterLim;
}
void        set_On_Off_State(bool state)
{
  if (state)
  {
      on_off    = true;
  }
  else
  on_off        = false;
}
bool        get_On_Off_State(void)
{
  return on_off;
}
void        set_rotorDirection(direction_t direction) 
{
  direction_g = direction;
}
direction_t get_rotorDirection(void) 
{
  return direction_g;
}
void        set_RedLED(bool on)
{
  if (on) {LL_GPIO_SetOutputPin(RED_LED_PORT, RED_LED_PIN);}
  else    {LL_GPIO_SetOutputPin(RED_LED_PORT, RED_LED_PIN);}
}
void        set_GreenLED(bool on)
{
  if (on) {LL_GPIO_SetOutputPin(GREEN_LED_PORT, GREEN_LED_PIN);}
  else    {LL_GPIO_SetOutputPin(GREEN_LED_PORT, GREEN_LED_PIN);}
}
void        set_YellowLED(bool on)
{
  if (on) {LL_GPIO_SetOutputPin(YELLOW_LED_PORT, YELLOW_LED_PIN);}
  else    {LL_GPIO_SetOutputPin(RED_LED_PORT, RED_LED_PIN);}
}

// UART-functions:
char *intToStrDec(uint32_t x, char *s)
{
    *--s = 0; // Decrement pointer and NULL terminate string
    if (!x) *--s = '0'; // Add a zero in ASCII if x is zero
    for (; x; x/=10) *--s = '0'+x%10; // Loop as long as x is not equal to zero, divide by 10 and add the remainder as the current digit
    // (remember that x/=10 is performed after the body x%10)
    return s; // Return a pointer to the beginning of the string (this does not have to be the beginning of the buffer)
}
void print_uint32(uint32_t val) {

    char buf[3*sizeof(uint32_t)+1];

    char *str = intToStrDec(val, buf + sizeof(buf));

    while(*str){
        while(!LL_USART_IsActiveFlag_TC(USART2));
        LL_USART_TransmitData8(USART2, *str++);
    }
}
void print_str(char *str){
    while(*str){
        while(!LL_USART_IsActiveFlag_TC(USART2));
        LL_USART_TransmitData8(USART2, *str++);
    }
}

float min(float x, float y, float z) 
{
  // Returns the lowest floating-point number among the three inputs.
  return x < y ? (x < z ? x : z) : (y < z ? y : z);
}
float max(float x, float y, float z) 
{
  // Returns the highest floating-point number among the three inputs.
  return x > y ? (x > z ? x : z) : (y > z ? y : z);
}

uint32_t get_encoder_timer_count(){
    return LL_TIM_GetCounter(TIM3);
}


//_______________________________________________________________________________________________________________________
// ISR-function for handling of timer-interrupt on TIM2:

void TIM2_IRQHandler(void)
{

  //LL_GPIO_SetOutputPin(TRIGGER_SIGNAL_PWM_PORT, TRIGGER_SIGNAL_PWM_PIN);

  // Parametre for PWM-algoritmer:
  scheme_t        algo       = get_ModulationAlgorithm();
  float           m_a        = get_AmplitudeModulationIndex();
  float           Vd         = get_Vd();
  uint32_t        k_reload   = LL_TIM_GetAutoReload(TIM1);
  uint32_t        sine_res   = 101;
  uint32_t        counterLim = get_InterruptCounterLimit();
  static uint32_t counter    = 0;

  if(counter >= counterLim)
  {

    static uint32_t i1 = 0;
    static uint32_t i2 = 67; //120 grader
    static uint32_t i3 = 34; //240 grader

    compare_t compare;
    float UAo1, UBo1, UCo1, Uk;

    switch (algo)
    {
      case SPWM:
          compare.L1 = (uint32_t)((m_a*k_reload*sine_table[i1] + k_reload)/2.0);
          compare.L2 = (uint32_t)((m_a*k_reload*sine_table[i2] + k_reload)/2.0);
          compare.L3 = (uint32_t)((m_a*k_reload*sine_table[i3] + k_reload)/2.0);
        break;


      case SVPWM:
          UAo1 = m_a*(Vd/sqrt(3))*sine_table[i1];
          UBo1 = m_a*(Vd/sqrt(3))*sine_table[i2];
          UCo1 = m_a*(Vd/sqrt(3))*sine_table[i3];
    
          Uk = (1/2.0)*(max(UAo1, UBo1, UCo1) + min(UAo1, UBo1, UCo1));

          compare.L1 = (uint32_t)(k_reload*((1/sqrt(3))*m_a*sine_table[i1]-(Uk/Vd)) + k_reload/2.0);
          compare.L2 = (uint32_t)(k_reload*((1/sqrt(3))*m_a*sine_table[i2]-(Uk/Vd)) + k_reload/2.0);
          compare.L3 = (uint32_t)(k_reload*((1/sqrt(3))*m_a*sine_table[i3]-(Uk/Vd)) + k_reload/2.0);
        break;

    default:
      break;
    }

    if (get_rotorDirection() == CCW) 
    { 
      uint32_t temp = compare.L2;
      compare.L2    = compare.L3;
      compare.L3    = temp;
    }

    // Set compare values:
    LL_TIM_OC_SetCompareCH1(TIM1, compare.L1);
    LL_TIM_OC_SetCompareCH2(TIM1, compare.L2);
    LL_TIM_OC_SetCompareCH3(TIM1, compare.L3);

    i1++; i2++; i3++;
   
    /*
    if (i1 >= sine_res) {
      LL_GPIO_TogglePin(TRIGGER_SIGNAL_PWM_PORT, TRIGGER_SIGNAL_PWM_PIN);
      i1 = 1;
    }*/
    if (i1 >= sine_res) {

      
  //Toggle for å trigge oscilloskop
  
   LL_GPIO_TogglePin(TRIGGER_SIGNAL_PWM_PORT, TRIGGER_SIGNAL_PWM_PIN);


      i1 = 1;
  }
  
    if (i2 >= sine_res) i2 = 1;
    if (i3 >= sine_res){
      i3 = 1;
    }

    counter = 0;

  }

  counter++;

  if (LL_TIM_IsActiveFlag_UPDATE(TIM2)) LL_TIM_ClearFlag_UPDATE(TIM2);


}



//_______________________________________________________________________________________________________________________
// MAIN FINCTION:


int main()
{
  // Initializations:
  initialize_SystemClock();
  initialize_TIM1();
  initialize_TIM2();
  initialize_EncoderTimer();
  enable_gpio_ports_clock();
  initialize_UART();
  initialize_IO();
  

  //Sett RST-pinnene høye for å aktivere gate driverene //V3
  LL_GPIO_SetOutputPin(DRIVER1_RST_PORT, DRIVER1_RST_PIN);  // PA3
  LL_GPIO_SetOutputPin(DRIVER2_RST_PORT, DRIVER2_RST_PIN);  // PB5
  LL_GPIO_SetOutputPin(DRIVER3_RST_PORT, DRIVER3_RST_PIN);  // PC0


  //__________________________________________________________________________________________________________________________________
  // SETTINGS 
  // (Må instilles korrekt av bruker):

  set_ModulationAlgorithm(SVPWM);               //       Ønsket modulasjonsalgoritme (SVPWM eller SPWM)
  set_SwitchingFrequency_Manually(5000);        // [Hz]  Ønsket svitsjefrekvens
  set_Vd(230);                                  // [V]   Påtrykt DC-link spenning
  double   nominal_MotorVoltage    = 230;       // [V]   Nominell linjespenning for motor (400V for stjerne, 230V for trekant)
  double   nominal_MotorFrequency  = 50;        // [Hz]  Nominell frekvens for motor
  uint32_t max_Frequency           = 100;       // [Hz]  Høyeste tillatte frekvens
  uint32_t min_Frequency           = 1;         // [Hz]  Laveste tillatte frekvens

  // Driftsmodus:
  uint32_t manualMode              = 1;      
  /*  manualMode avgjør hvilke driftsmodus omformeren opererer i:
  *     - Hvis manualMode = 1  ->  modulasjonsfrekens og ma settes konstant til de manuelle instullingene, dreieretning kan ikke endres
  *     - Hvis manualMode = 0  ->  modulasjonsfrekvens styres av encoder med U/f = konst, dreieretning på rotor styres av DIR-knapp
  */ 

  //__________________________________________________________________________________________________________________________________




  switch(manualMode)
  {
    case 1:
      set_AmplitudeModulationIndex(1.0);
      set_ModulationFrequency_Manually(50);
      break;

    case 0:
      LL_TIM_SetPrescaler(TIM2, 8);
      LL_TIM_SetAutoReload(TIM2, 100);
      break;

    default:
    break;
  }

  // Enable counters:
  LL_TIM_EnableCounter(TIM2);
  LL_TIM_EnableCounter(TIM1);

  uint16_t prev_encoder_Val   = 0;

  // Dynamiske variabler:
  float    V_DC;                                  // DC-link voltage
  float    curr_ma;                               // Modulation index
  uint32_t curr_f             = 1;                // Set current frequency to minimal value at first

// Infinite loop:
for(;;)
{
    read_OnOffButton();
    V_DC = get_Vd();               

    // Få inn modulasjonsfrekvens fra encoder:
    uint32_t encoder_Val    = get_encoder_timer_count();       // Får telle-verdien til TIM3
    if(encoder_Val > prev_encoder_Val) {curr_f--;}             // Encoder har rotert mot høyre
    if(encoder_Val < prev_encoder_Val) {curr_f++;}             // Encoder har rotert mot venstre¨
    prev_encoder_Val = encoder_Val;

    // Skaler modulasjonsfrekvens til å ligge i riktig intervall
    if(curr_f > max_Frequency)     {curr_f = max_Frequency;}
    if(curr_f < min_Frequency + 1) {curr_f = min_Frequency;}

    // Kontroller modulasjonsfrevkens fra encoder dersom driftsmodus ikke er i manuelt mode
    if(manualMode == 0)
    {
      // Beregn ma basert på ønsket modulasjonsfrekvens slik at U/f holdes konstant
      curr_ma = calculate_AmplitudeModulationIndex(curr_f, V_DC, nominal_MotorFrequency, nominal_MotorVoltage);
      set_AmplitudeModulationIndex(curr_ma);

      // Beregn interrupt-counter basert på øsnket modulasjonsfrekvens
      set_InterruptCounterLimit(curr_f);

      read_DirectionButton();
    }

    
    print_uint32(curr_f);
    print_str("\n");
    
  }
}



//______________________________________________________________________________________________________________________
// Calcultatios

// SPWM calculations:
uint32_t    calculate_MaximunFrequency_SPWM(double Vd, double f_n, double V_n)
{
  // Returns the maximum frequency before overmodulation (m_a > 1)
  double k          = 1*sqrt(3)/(2*sqrt(2));
  uint32_t f_max    = k*Vd*f_n/V_n;
  return f_max;
}
double calculate_AmplitudeModulationIndex(uint32_t curr_f, double curr_Vd, double f_n, double V_n)
{
  // Calculate linear modulation-index
  double m_a;
  double k    = 2*sqrt(2)/sqrt(3);                 // Constant
  m_a         = k*V_n*curr_f/(curr_Vd*f_n);        // Actual calcutation

  if(m_a > 0)
    {
      return m_a;
    }

    if (m_a < 0)
      {
        return 0;     
      }
}



//_______________________________________________________________________________________________________________________
// Configurations and initializations:

// Initialiseringsfunksjoner:
void initialize_SystemClock(){

  LL_FLASH_SetLatency(LL_FLASH_LATENCY_4);
  while(LL_FLASH_GetLatency()!= LL_FLASH_LATENCY_4){
  }

  LL_PWR_SetRegulVoltageScaling(LL_PWR_REGU_VOLTAGE_SCALE1);
  LL_RCC_HSI_Enable();

   /* Wait till HSI is Ready */
  while(LL_RCC_HSI_IsReady() != 1){
  }

  LL_RCC_HSI_SetCalibTrimming(16);

  LL_RCC_PLL_ConfigDomain_SYS(LL_RCC_PLLSOURCE_HSI, LL_RCC_PLLM_DIV_1, 10, LL_RCC_PLLR_DIV_2);
  LL_RCC_PLL_EnableDomain_SYS();
  LL_RCC_PLL_Enable();

   /* Wait till PLL is Ready */
  while(LL_RCC_PLL_IsReady() != 1){
  }
  LL_RCC_SetSysClkSource(LL_RCC_SYS_CLKSOURCE_PLL);

   /* Wait till System Clock is Ready */
  while(LL_RCC_GetSysClkSource() != LL_RCC_SYS_CLKSOURCE_STATUS_PLL){
  }

  LL_RCC_SetAHBPrescaler(LL_RCC_SYSCLK_DIV_1);
  LL_RCC_SetAPB1Prescaler(LL_RCC_APB1_DIV_1);
  LL_RCC_SetAPB2Prescaler(LL_RCC_APB2_DIV_1);

  LL_Init1msTick(80000000); // 80 MHz

  LL_SetSystemCoreClock(80000000); // 80 MHz

  SysTick_Config(SystemCoreClock / 1000);
}
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

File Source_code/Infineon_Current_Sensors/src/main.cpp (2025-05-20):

//**********************************************************************************************************************//
//** Dene filen inneholder programvare utviklet av Fredrik Larsgård, Kristian Farnes og Jan Magnus Botnene våren 2025©**//
//**********************************************************************************************************************//

#include <Arduino.h>
#include <stdio.h>
#include <string.h> 
#include "stm32l4xx_ll_adc.h"
#include "stm32l4xx_ll_usart.h"
#include "stm32l4xx_ll_gpio.h"
#include "stm32l4xx_ll_bus.h"
#include "stm32l4xx_ll_utils.h"
#include "stm32l4xx_ll_rcc.h" //Må inkluderes for å bruke  LL_RCC_SetADCClockSource(LL_RCC_ADC_CLKSOURCE_SYSCLK);

// **Prototyper**
void MX_GPIO_Init(void);
void MX_USART2_UART_Init(void);
void send_uart(const char *message);
void calibrate_adc();
void init_adc();
void LL_systemklokke_setup();
uint32_t LL_systemklokke_tid();
uint32_t filter_adc_fast_ema(int index, uint32_t ny_ADC_sample);
uint32_t read_ADC(void);
//Vaiabler
 uint32_t adc_values[3];  
 uint32_t voltage[3];       
 int current[3];
 uint32_t filtered_adc_value[3]; //variabel for filter. setter startverdi for ca 0 ampere. 
 uint32_t filtered_voltage[3]; 
 int filtered_current[3];
 float S_L1 =0.0537; //Orginalt 0,048
 float S_L2 =0.0548; //Orginalt 0,0537
 float S_L3 = 0.0544; //Sensitivitets koefisient. Orginalt 0.0557
 float U_reff = 1.6561; //referanse volt, måles før oppstart
 float S_justert = S_L3*(U_reff/1.65);
 uint32_t system_tid ;
 uint32_t forige_system_tid;
 char buffer[150];

int main(void) {
    init();  // Initialiserer serieporten for Arduino framework, viktig for å kunne sende noe vi Serial porten
    MX_USART2_UART_Init(); // initialisere funskjon
    read_ADC();// initialiserer funkso
    calibrate_adc();
    init_adc();
    LL_systemklokke_setup();
    LL_systemklokke_tid();
    // MX_GPIO_Init(); //initialiserer funksjon
    //MX_ADC1_Init(); //

    // **Sjekk systemklokke**
    char clock_buffer[50];
    sprintf(clock_buffer, "Clock: %lu\r\n", SystemCoreClock);
    send_uart(clock_buffer);
     LL_GPIO_SetOutputPin(GPIOA, LL_GPIO_PIN_0);

   

    while (1) { 
        system_tid = LL_systemklokke_tid();

        adc_values[0] = read_ADC();
        adc_values[1] = read_ADC();
        adc_values[2] = read_ADC();
        
        //Rgner ut strøm for L1
        filtered_adc_value[0] = filter_adc_fast_ema(0,adc_values[0]);
        voltage[0] = ((adc_values[0]*3.3 *1000)/4095)+50;//Legger til noen milivolt for at det skal samsvare med spenningen som chippen gir ut ved 0 A
        current[0] = ((voltage[0]-(U_reff*1000))/S_L1);
        filtered_voltage[0] = ((filtered_adc_value[0]*3.3 *1000)/4095)+58; //Brukte 40 mV på L3, 54 mv L2, 58 mV L1
        filtered_current[0] = ((filtered_voltage[0]-(U_reff*1000))/S_L1);
          //Rgner ut strøm for L2
        filtered_adc_value[1] = filter_adc_fast_ema(1, adc_values[1]);
        voltage[1] = ((adc_values[1]*3.3 *1000)/4095)+50;//Legger til noen milivolt for at det skal samsvare med spenningen som chippen gir ut ved 0 A
        current[1] = ((voltage[1]-(U_reff*1000))/S_L2);
        filtered_voltage[1] = ((filtered_adc_value[1]*3.3 *1000)/4095)+54; //Brukte 40 mV på L3, 54 mv L2, 58 mV L1
        filtered_current[1] = ((filtered_voltage[1]-(U_reff*1000))/S_L2);
          //Rgner ut strøm for L3
        filtered_adc_value[2] = filter_adc_fast_ema(2, adc_values[2]);
        voltage[2] = ((adc_values[2]*3.3 *1000)/4095)+50;//Legger til noen milivolt for at det skal samsvare med spenningen som chippen gir ut ved 0 A
        current[2] = ((voltage[2]-(U_reff*1000))/S_L3);
        filtered_voltage[2] = ((filtered_adc_value[2]*3.3 *1000)/4095)+44; 
        filtered_current[2] = ((filtered_voltage[2]-(U_reff*1000))/S_L3);
        
        if (system_tid-forige_system_tid>4000) { //2000 ser ut til å tilsvare et sekund
        //
        for (int i = 0; i < 3; i++) {
        sprintf(buffer,
        "ADC L%d: %lu, Spenning L%d: %lumV, Strøm L%d: %d mA, "
        "Filtrert ADC L%d: %lu, Filtrert spenning L%d: %lu mV, Filtrert strøm L%d: %d mA\r\n",
        i+1, adc_values[i],
        i+1, voltage[i],
        i+1, current[i],
        i+1, (uint32_t)filtered_adc_value[i],
        i+1, filtered_voltage[i],
        i+1, filtered_current[i]
         );
         send_uart(buffer);
        }
        send_uart("\r\n"); //Linjeskift for hver iterasjon
        forige_system_tid = LL_systemklokke_tid();   
        }   
    }
}
//Aktiverer en systemklokke. Bruker TIM6 til dette
void LL_systemklokke_setup(){
LL_APB1_GRP1_EnableClock(LL_APB1_GRP1_PERIPH_TIM6);
// Forutsetter at systemklokke er 80 MHz – juster om din er annerledes
//LL_TIM_SetPrescaler(TIM6, (SystemCoreClock));  // (80 MHz *2 = 2000 Hz) → 0,5 ms per tick 
LL_TIM_SetPrescaler(TIM6, 80000 - 1);  // 80 MHz / 80000 = 1000 Hz = 1 ms per tick
LL_TIM_SetAutoReload(TIM6, 0xFFFF); // Maks 65535 ms (kan også bruke 32-bit timer)
LL_TIM_SetCounterMode(TIM6, LL_TIM_COUNTERMODE_UP);
LL_TIM_EnableCounter(TIM6);
}
//henter verdi til system klokke
uint32_t LL_systemklokke_tid(){
return LL_TIM_GetCounter(TIM6);
}


//Funksjon for software filter
float ema_internal[3] = {0.0f, 0.0f, 0.0f};  // tre forskjellige interne flytvallvaribler for tre mplinger

uint32_t filter_adc_fast_ema(int index, uint32_t ny_ADC_sample) {
    const float alpha = 0.0001f; //Juster denne for å gjre filteret mer nøyaktig, orginalt 0.1. Lavere verdi filtrerer mer støy
    ema_internal[index] = alpha * ny_ADC_sample + (1.0f - alpha) * ema_internal[index];
    return (uint32_t)(ema_internal[index] + 0.5f);  // avrund til nærmeste heltall
}
// **USART2-konfigurasjon** 

void MX_USART2_UART_Init(void) {
    LL_APB1_GRP1_EnableClock(LL_APB1_GRP1_PERIPH_USART2);
    LL_AHB2_GRP1_EnableClock(LL_AHB2_GRP1_PERIPH_GPIOA);

    LL_GPIO_InitTypeDef GPIO_InitStruct = {0};
    GPIO_InitStruct.Pin = LL_GPIO_PIN_2 | LL_GPIO_PIN_3;
    GPIO_InitStruct.Mode = LL_GPIO_MODE_ALTERNATE;
    GPIO_InitStruct.Alternate = LL_GPIO_AF_7;
    GPIO_InitStruct.Speed = LL_GPIO_SPEED_FREQ_HIGH;
    GPIO_InitStruct.OutputType = LL_GPIO_OUTPUT_PUSHPULL;
    GPIO_InitStruct.Pull = LL_GPIO_PULL_NO;
    LL_GPIO_Init(GPIOA, &GPIO_InitStruct);

    // Sett baudrate til riktig frekvens
    LL_USART_SetBaudRate(USART2, HAL_RCC_GetHCLKFreq(), LL_USART_OVERSAMPLING_16, 115200);
    LL_USART_SetDataWidth(USART2, LL_USART_DATAWIDTH_8B);
    LL_USART_SetStopBitsLength(USART2, LL_USART_STOPBITS_1);
    LL_USART_SetParity(USART2, LL_USART_PARITY_NONE);
    LL_USART_SetTransferDirection(USART2, LL_USART_DIRECTION_TX_RX);
    LL_USART_Enable(USART2);

    // Sørg for at TX-linjen er aktiv
    LL_USART_EnableDirectionTx(USART2);

    send_uart("USART2 Initialized\r\n");  // Testmelding
}
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

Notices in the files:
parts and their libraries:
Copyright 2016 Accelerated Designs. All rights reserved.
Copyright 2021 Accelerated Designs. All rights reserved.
